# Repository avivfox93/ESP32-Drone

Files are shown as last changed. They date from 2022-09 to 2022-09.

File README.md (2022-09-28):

## ESP32-Drone Hardware

### Introduction

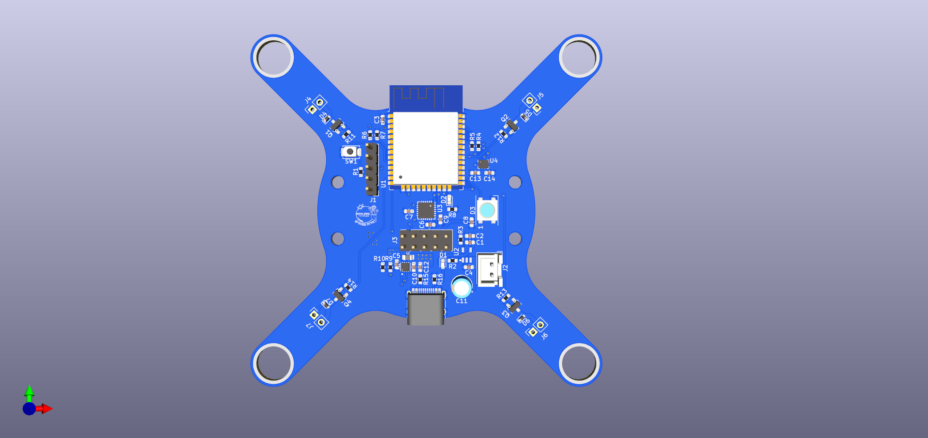
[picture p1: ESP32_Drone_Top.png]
ESP32-Drone-Top

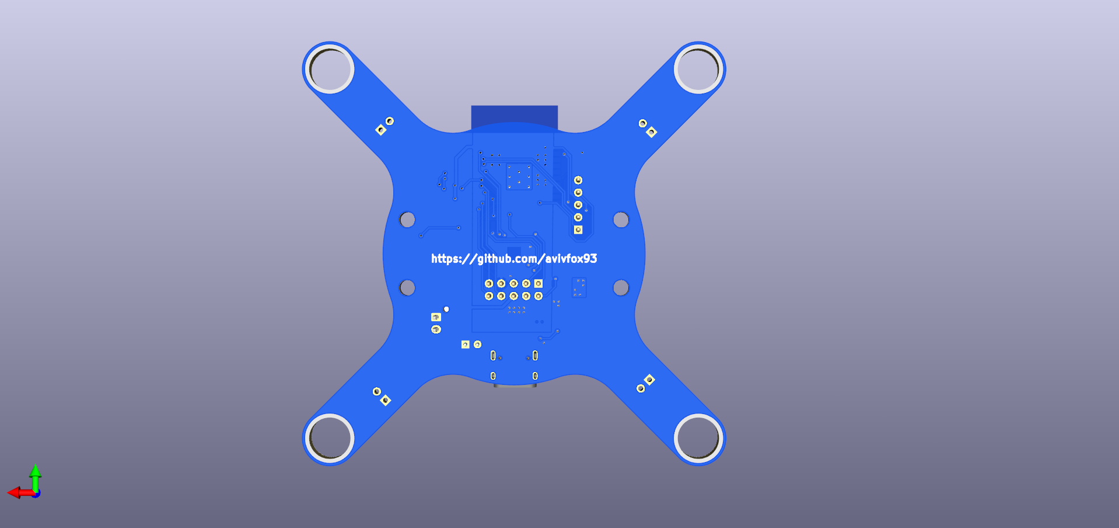
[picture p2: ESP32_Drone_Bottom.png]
ESP32-Drone-Bottom


Hardware design for drone based of ESP32 and BME6050. It desinged using KiCad 6. Parts chosen for both low cost and stocks availability.

### Features

1. ESP32 MCU
2. MPU6050 IMU
3. BMP280 barometer
4. LiPo charger
5. WS2812b indication LED
6. External peripherals extension connector
7. On board 8mm motor sockets

### Remarks
1. Better to manufacure PCB 1.0 mm in thickness
2. Better to solder the motor on both sides, motors might tear the copper layer if its not soldered well

### Firmware
Can be used with my fork of ESP-Drone (based on Crazyflie) -> https://github.com/avivfox93/esp-drone

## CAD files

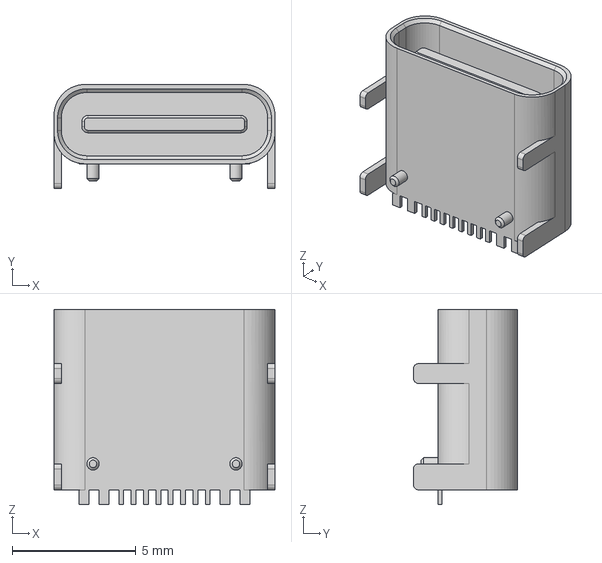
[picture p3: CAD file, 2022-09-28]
models/HRO TYPE-C-31-M-12.step
8.94 x 4.21 x 7.90 mm

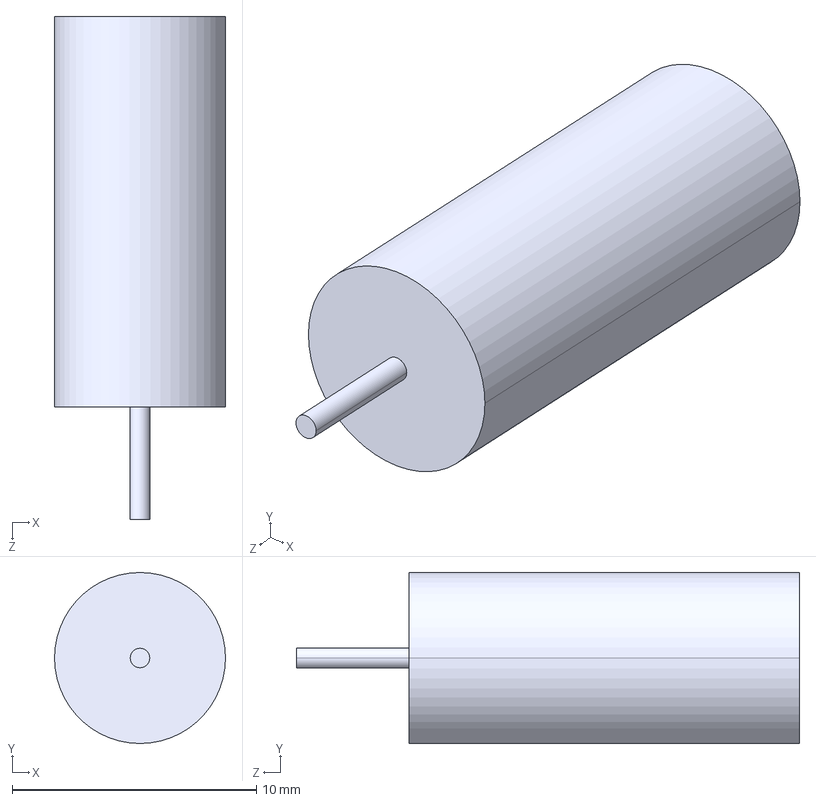
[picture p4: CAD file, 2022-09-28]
models/Motor.STEP
7.00 x 7.00 x 20.6 mm

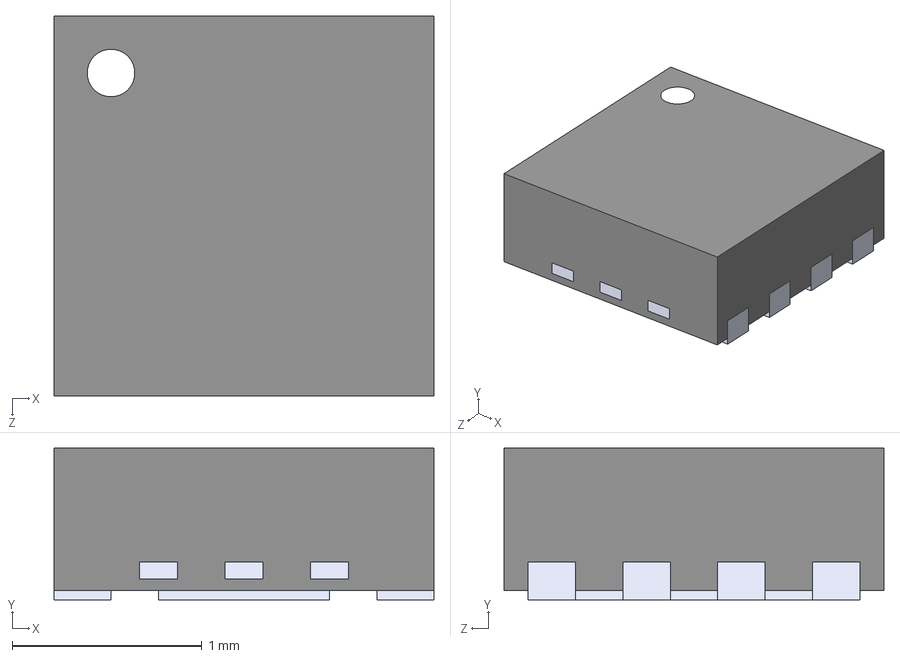
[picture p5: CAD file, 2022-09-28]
models/TPS62082DSGT.step
2.00 x 0.8 x 2.00 mm

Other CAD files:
models/Motor.STL

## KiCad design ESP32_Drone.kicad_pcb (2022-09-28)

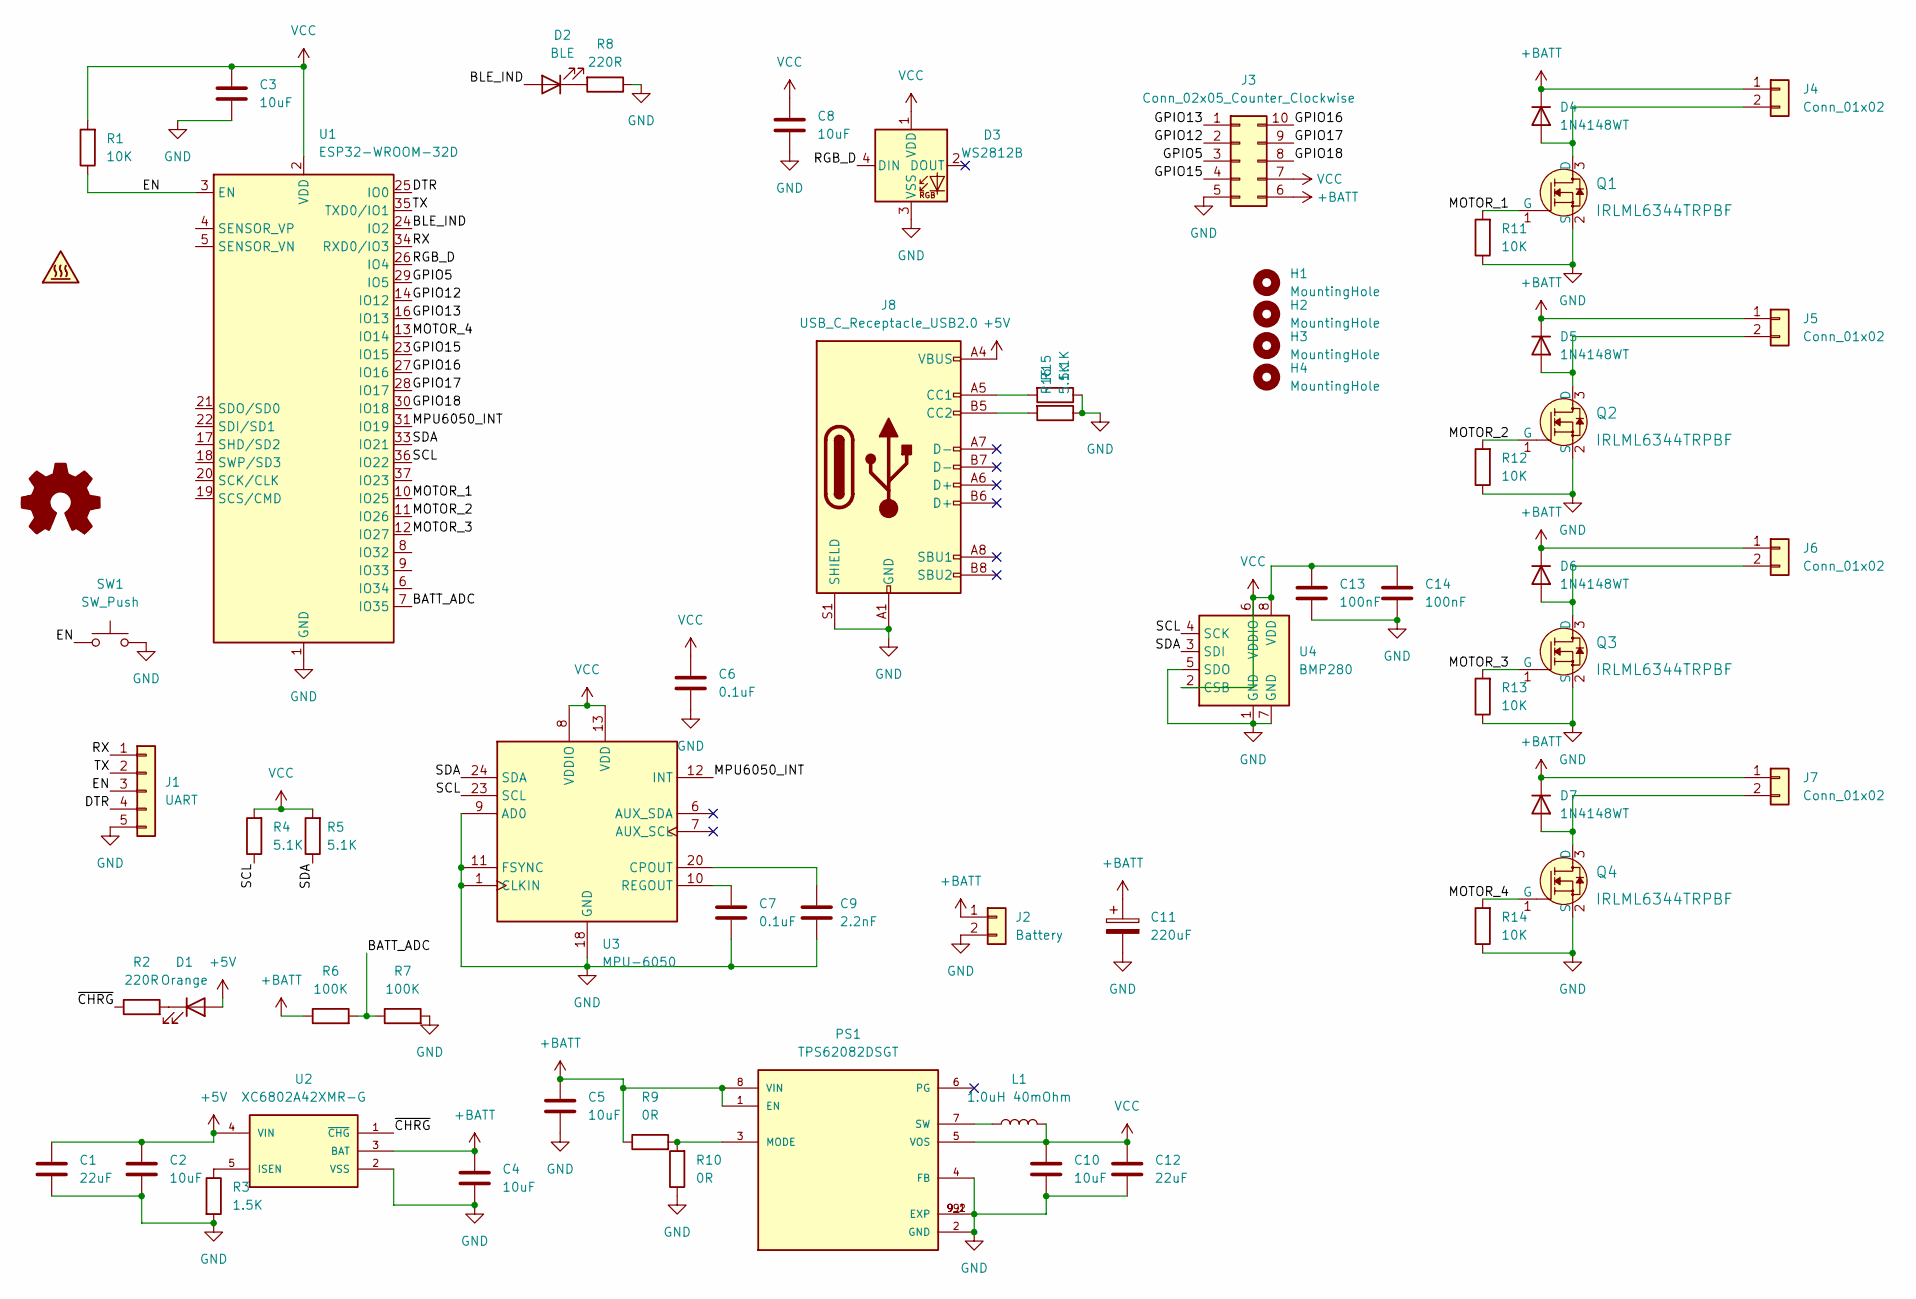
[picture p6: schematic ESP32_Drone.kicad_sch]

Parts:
C1, C12: 22uF; C_0603_1608Metric
C2, C3, C4, C5, C8, C10: 10uF; C_0603_1608Metric
C6, C7: 0.1uF; C_0603_1608Metric
C9: 2.2nF; C_0603_1608Metric
C11: 220uF; CP_Radial_D5.0mm_P2.50mm
C13, C14: 100nF; C_0603_1608Metric
D1: Orange; LED_0603_1608Metric
D2: BLE; LED_0603_1608Metric
D3: WS2812B; LED_WS2812B_PLCC4_5.0x5.0mm_P3.2mm
D4, D5, D6, D7: 1N4148WT; D_SOD-523
H1, H2, H3, H4: MountingHole; MountingHole_3.2mm_M3
J1: UART; PinHeader_1x05_P2.54mm_Vertical
J2: Battery; JST_XH_B2B-XH-AM_1x02_P2.50mm_Vertical
J3: Conn_02x05_Counter_Clockwise; PinSocket_2x05_P2.54mm_Vertical
J4, J5, J6, J7: Conn_01x02; PinSocket_1x02_P2.54mm_Vertical
J8: USB_C_Receptacle_USB2.0; USB_C_Receptacle_HRO_TYPE-C-31-M-12
L1: 1.0uH 40mOhm; L_0805_2012Metric
LOGO1: Logo_Open_Hardware_Small; meshek_fox_logo.kicad_5.9X6.0_mod
PS1: TPS62082DSGT; CONV_TPS62082DSGT; PARTREV NOVEMBER 2016
Q1, Q2, Q3, Q4: IRLML6344TRPBF; SOT-23-3; MPN IRLML6344TRPBF; Digi-Key_PN IRLML6344TRPBFCT-ND
R1, R11, R12, R13, R14: 10K; R_0603_1608Metric
R2, R8: 220R; R_0603_1608Metric
R3: 1.5K; R_0603_1608Metric
R4, R5, R15, R16: 5.1K; R_0603_1608Metric
R6, R7: 100K; R_0603_1608Metric
R9, R10: 0R; R_0603_1608Metric
SW1: SW_Push; SW_Push_SPST_NO_Alps_SKRK
SYM1: SYM_Hot_Small; PCB Drone Edgecuts
U1: ESP32-WROOM-32D; ESP32-WROOM-32
U2: XC6802A42XMR-G; SOT95P280X130-5N
U3: MPU-6050; InvenSense_QFN-24_4x4mm_P0.5mm
U4: BMP280; Bosch_LGA-8_2x2.5mm_P0.65mm_ClockwisePinNumbering

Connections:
+5V: C1.1, C2.1, D1.2 (A), J8.A4 (VBUS), J8.A9 (VBUS), J8.B4 (VBUS), J8.B9 (VBUS), U2.4 (VIN)
+BATT: C4.1, C5.1, C11.1, D4.1 (K), D5.1 (K), D6.1 (K), D7.1 (K), J2.1, J3.6, J4.1, J5.1, J6.1, J7.1, PS1.1 (EN), PS1.8 (VIN), R6.1, R9.1, U2.3 (BAT)
/BATT_ADC: R6.2, R7.1, U1.7 (IO35)
/BLE_IND: D2.2 (A), U1.24 (IO2)
/DTR: J1.4, U1.25 (IO0)
/EN: J1.3, R1.1, SW1.1, U1.3 (EN)
/GPIO5: J3.3, U1.29 (IO5)
/GPIO12: J3.2, U1.14 (IO12)
/GPIO13: J3.1, U1.16 (IO13)
/GPIO15: J3.4, U1.23 (IO15)
/GPIO16: J3.10, U1.27 (IO16)
/GPIO17: J3.9, U1.28 (IO17)
/GPIO18: J3.8, U1.30 (IO18)
/MOTOR_1: Q1.1 (G), R11.2, U1.10 (IO25)
/MOTOR_2: Q2.1 (G), R12.2, U1.11 (IO26)
/MOTOR_3: Q3.1 (G), R13.2, U1.12 (IO27)
/MOTOR_4: Q4.1 (G), R14.2, U1.13 (IO14)
/MPU6050_INT: U1.31 (IO19), U3.12 (INT)
/RGB_D: D3.4 (DIN), U1.26 (IO4)
/RX: J1.1, U1.34 (RXD0/IO3)
/SCL: R4.1, U1.36 (IO22), U3.23 (SCL), U4.4 (SCK)
/SDA: R5.1, U1.33 (IO21), U3.24 (SDA), U4.3 (SDI)
/TX: J1.2, U1.35 (TXD0/IO1)
/~CHRG: R2.1, U2.1 (~CHG)
GND: C1.2, C2.2, C3.2, C4.2, C5.2, C6.2, C7.2, C8.2, C9.2, C10.2, C11.2, C12.2, C13.2, C14.2, D3.3 (VSS), J1.5, J2.2, J3.5, J8.A1 (GND), J8.A12 (GND), J8.B1 (GND), J8.B12 (GND), J8.S1 (SHIELD), PS1.2 (GND), PS1.4 (FB), PS1.9 (EXP), PS1.9_1 (EXP), PS1.9_2 (EXP), Q1.2 (S), Q2.2 (S), Q3.2 (S), Q4.2 (S), R3.2, R7.2, R8.1, R10.1, R11.1, R12.1, R13.1, R14.1, R15.1, R16.1, SW1.2, U1.1 (GND), U1.15 (GND), U1.38 (GND), U1.39 (GND), U2.2 (VSS), U3.1 (CLKIN), U3.9 (AD0), U3.11 (FSYNC), U3.18 (GND), U4.1 (GND), U4.5 (SDO), U4.7 (GND)
unnamed: C7.1, U3.10 (REGOUT)
unnamed: C9.1, U3.20 (CPOUT)
unnamed: D1.1 (K), R2.2
unnamed: D2.1 (K), R8.2
unnamed: D4.2 (A), J4.2, Q1.3 (D)
unnamed: D5.2 (A), J5.2, Q2.3 (D)
unnamed: D6.2 (A), J6.2, Q3.3 (D)
unnamed: D7.2 (A), J7.2, Q4.3 (D)
unnamed: J8.A5 (CC1), R15.2
unnamed: J8.B5 (CC2), R16.2
unnamed: L1.1, PS1.7 (SW)
unnamed: PS1.3 (MODE), R9.2, R10.2
unnamed: R3.1, U2.5 (ISEN)
VCC: C3.1, C6.1, C8.1, C10.1, C12.1, C13.1, C14.1, D3.1 (VDD), J3.7, L1.2, PS1.5 (VOS), R1.2, R4.2, R5.2, U1.2 (VDD), U3.8 (VDDIO), U3.13 (VDD), U4.2 (CSB), U4.6 (VDDIO), U4.8 (VDD)

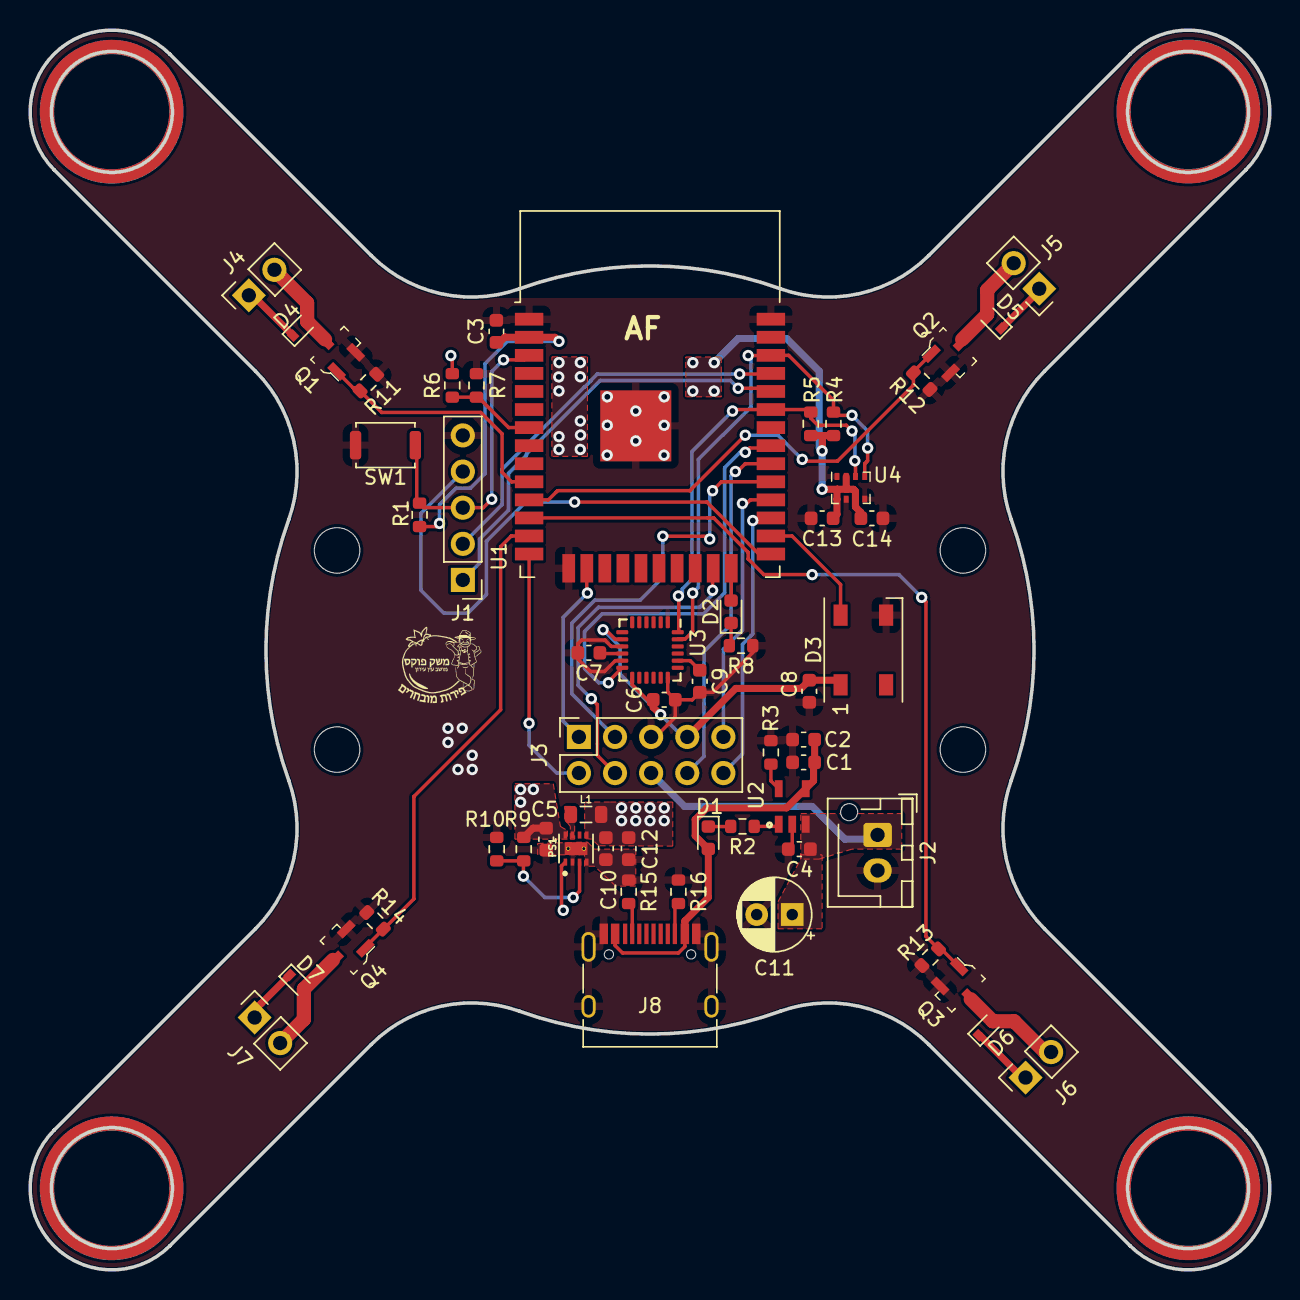
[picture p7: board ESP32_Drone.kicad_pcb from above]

Board: 2 copper layers, 87.1 x 87.1 mm, 62 parts (0 on the bottom side), 39 nets.
